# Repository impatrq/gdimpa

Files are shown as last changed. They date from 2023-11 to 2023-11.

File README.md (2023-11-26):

<div align="center">

# *GDIMPA*

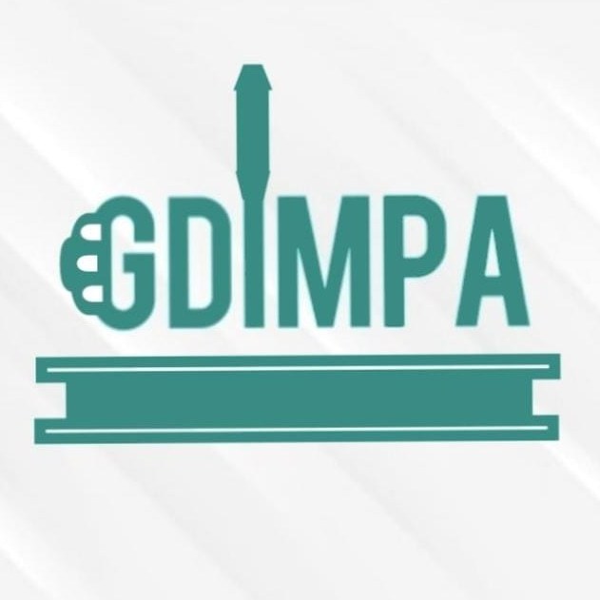
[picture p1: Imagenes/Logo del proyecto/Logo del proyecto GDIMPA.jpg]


&nbsp;

| Página web | linkedin | Instagram |
|---|---|---|
|[Mira nuestra pagina de Webnode](https://gdimpa-project-0.webnode.page)|[Búscanos en linkedin](https://www.linkedin.com/in/gd-impa-8b2537271/)|[También mira nuestro Instagram](https://www.instagram.com/GD.IMPA/?hl=es-la<%2Fp>)|

&nbsp;

</div>

## Objetivo:

Nuestro objetivo es la _modernización y puesta a punto_ de un _Grupo Electrógeno Diésel antiguo_, con esto buscamos brindar una forma _barata y sencilla_ de darle una nueva vida útil a estos equipos costosos, que no sean modernos, automatizándolos, de esta manera _controlar y monitorear_ el correcto funcionamiento de estos equipos.

## Descrición General:

*GDIMPA* es un sistema con la finalidad de _automatizar y monitorear_ de un generador eléctrico antiguo, el cual consta de la implementación de tres sensores:
- Un bulbo de temperatura: el cual es el encargado de medir la temperatura del motor, 
- Un bulbo de presión de aceite: el cual se encargade verificar si la presión del motor es la adecuada, 
- Un sensor de temperatura ambiental: el cual sirve para verificar si la temperatura ambiente es demasiado baja para que el motor encienda.

Todos los parámetros serán controlados en el tablero por dos PLC LOGO! 8, los cuales trabajan en conjunto para brindar una mayor capacidad de entradas tanto analógicas como digitales
Además se estará midiendo constantemente el amperaje y el voltaje generado, esto para ver que el equipo no esté trabajando de forma forzada.

El programa del PLC está hecho para controlar todos los parámetros y funciones de automatización, como el encendido automático, alarmas en caso de que la temperatura sea demasiado alta o la presión de aceite sea demasiado baja.

## Alcance:

El desarrollo de este sistema abarca a todas las industrias y personas que tengan un grupo electrógeno antiguo, pero que su funcionamiento aun sea bueno como un equipo auxiliar en caso de un corte en el suministro de corriente eléctrica, pero que al ser un equipo viejo no termine siendo práctico su uso. Sumándole a esto el hecho de que es más barato que el reemplazo total del equipo por uno nuevo con un panel automatizado.

## Tecnologías utilizadas

### sistemas embedidos

- PLC LOGO! 8

### Placas de desarrollo

- Arduino uno

### Software utilizados para el desarrollo

- LOGO!Soft Comfort v8.3
- Arduino IDE 2.1.1 (bibliotecas usadas Wire.h y LiquidCrystal_I2C.h)
- proteus 8
- CADE SIMU

### Página web

- webnode

### Periféricos utilizados

- Lm317t
- Lm324
- Lm35
- Relés
- Tetrapolar 4x25
- Contactor

### Planos

- AutoCAD

## ¿Quiénes somos?

Somos un grupo de alumnos de 7mo 1ra avionica de la E.E.S.T. N°7 "Taller Regional Quilmes" (IMPA).

## Integrantes

<div align="center">

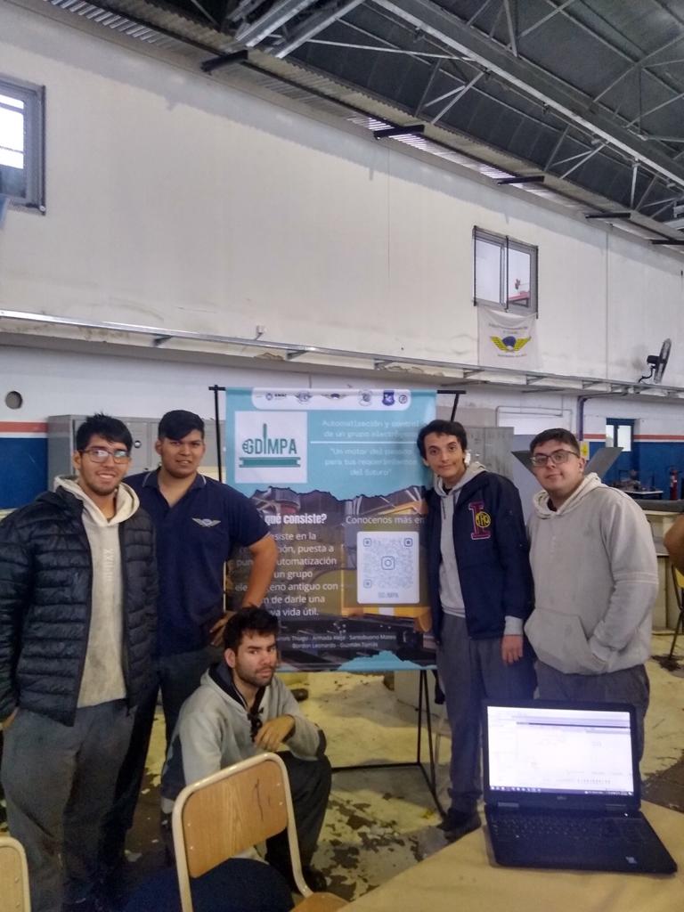
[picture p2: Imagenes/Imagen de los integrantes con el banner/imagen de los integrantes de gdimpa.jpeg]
Imagen de integrantes del proyecto


</div>

(De izquierda a derecha)

### Martins Thiago Ariel. 
Linkedin: (https://www.linkedin.com/in/thiago-a-martins/)

### Bordon Leonardo Agustin Caparros.
Linkedin: (https://www.linkedin.com/in/mateo-santobuono/?originalSubdomain=ar)

### Guzman Tomas Ignacio.
Linkedin: (https://www.linkedin.com/in/tomasignacio-guzman-9b542928a/)

### Armada Alejo.
Linkedin: (https://www.linkedin.com/in/alejo-armada/?originalSubdomain=ar)

### Santobuono Mateo Ruben.
Linkedin: (https://www.linkedin.com/in/mateo-santobuono/?originalSubdomain=ar)
****

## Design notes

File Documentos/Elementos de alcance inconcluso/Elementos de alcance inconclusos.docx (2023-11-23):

Elementos de alcance inconclusos

En este documento se encuentran todas las tareas las cuales teníamos pensado realizar y por diversas razones (ya sea falta de conocimientos, falta de tiempo, etc.) no se llegaron a completar:

- Reparación de la bomba inyectora: Desde principio de año hemos tenido problemas con la misma, fue el enfoque principal de trabajo durante la mayor parte del año. En un inicio al estar esta trabada la desarmamos y limpiamos, aunque a esta le rompimos una pieza gracias a la ayuda de un profesor se realizo una copia a medida, cuando la montamos esta no generaba suficiente presión y debido a falta tanto de conocimientos como de tiempo no fuimos capaces de ponerla en funcionamiento.
- Puesta en marcha del grupo electrógeno: Debido a que la bomba inyectora no se encontraba en condiciones, no emos sido capaces de poner en marcha el grupo electrógeno.
- Pantallas led: Debido al tiempo no tuvimos el tiempo de poner todas las pantallas en el tablero y tampoco de programarlas, tenemos las pantallas que fueron compradas por cooperadora.
- Bulbo de presión de aceite: Este componente lo tenemos desde principio de año, pero por mala gestión de nuestro tiempo no lo emos podido instalar en el sistema de aceite del propio motor, aunque se encuentra prácticamente cableado y listo para su instalación.
- Válvula electrónica para controlar el paso de combustible a la entrada de aire: Esta válvula era una idea originalmente concebida con el fin de hacer aun mas automático el sistema de calentamiento del motor, pero no nos concentramos en eso, aunque terminamos de cablear el sistema de timer para el calentamiento de la toma de aire.
- Control de zonas por prioridad: esta parte se encuentra programada, pero por la falta de tiempo no pudimos llevar el sistema al cableado, además de que las salidas del plc 2 fueron completamente usadas.
- Alarma de emergencia y botón para reiniciarla: El sistema se encuentra programado, e incluso hay una salida guardada para este sistema, la limitante es que no nos alcanzo el tiempo para agujerear el tablero y que nos faltó conseguir la luz.
- Bulbo de temperatura: este esta montado, pero falta el cableado, por que un día antes de la feria alguien rompió los cables que se encontraban unidos al bulbo.
- Los soportes para los trasformadores en el tablero: estos no fueron realizados, por falta de tiempo
- Realizar una estructura de protección: No la realizamos por falta de tiempo.
- Prendido completamente automático: Debido a limitaciones mecánicas no pudimos hacer 100% automático el encendido del motor.
- Incorporación de ruedas: Esta idea fue una que desde un inicio estuvo presente, aunque no fue nuestra prioridad y por eso no nos alcanzo el tiempo para terminarla.
- Apagado automático: Por falta de conocimientos sobre motores y también de tiempo, no logramos realizar esta idea, sino que fue reemplazada por una alarma en pantalla que muestra que se debe apagar el motor.
- Armado de los inyectores: Estos fueron sacados para su mantenimiento, y después por los problemas en la bomba no fue concretada su colocación.
- Cableado del interruptor de cambio de neutro para medición de los ojos de buey: Estos fueron colocados, pero no fueron cableados por escaso tiempo antes de la finalización de las partes.

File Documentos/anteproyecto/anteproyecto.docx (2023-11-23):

GDIMPA

GDIMPA:Este nombre fue elegido por el siguiente significado: Generador Diesel IMPA

Integrantes:

- Mateo santobuono
- Leonardo Bordon Caparros
- Tomas Ignacio Guzmán
- Alejo Armada
- Thiago Martins

Objetivo del proyecto:

Nuestro objetivo es proporcionar a la escuela con la capacidad de poder continuar con las actividades que requieran de electricidad en el caso de un apagón. Para lograr esto, restauraremos un generador diésel para que pueda volver a utilizarse como generador de energía de emergencia. También modernizaremos dicho generador para que este se prenda automáticamente desde el panel en el caso de un apagón y que pueda priorizar entre diferentes aparatos electrónicos a alimentar si es que no tiene la capacidad de alimentar a todos.

Utilidades del proyecto:

En el caso de un apagón, la escuela se vería incapaz de continuar con la enseñanza de ciertas materias que requieran de instrumentos electrónicos, tales como los osciloscopios, (Aquí hay que agregar más ejemplos), ect. Nuestro proyecto otorgaría la capacidad a la escuela de continuar con dichas enseñanzas sin ser interrumpida.

Descripción de funcionamiento

Nosotros proponemos como solución un sistema que mediante el uso de un PLC conectado a un motor diesel con un generador que proporcione energía a la escuela en el caso de un apagón o falta de energía.

Para lograr esto utilizaremos un Siemens LOGO! 8.2 que a través de varios voltímetros detectará si se ha producido un corte de luz para activar automáticamente desde el panel el motor diesel a través del generador, primero sensara la temperatura ambiente y en caso de ser necesario se activará el temporizador que calentará el aire para facilitar el encendido del motor.

La gestión de energía se realizará a través del programa del PLC que tendrá divisiones entre zonas más o menos prescindibles en el caso de que no sea posible alimentar a todas las zonas. Todo esto se mostrará en un panel de control, junto a los demás parámetros del motor. La temperatura del motor será leída a través de un sensor de temperatura y el nivel de combustible será leído con un sensor flotante.

Análisis de factibilidad:

El GDIMPA es un generador diésel que consta de un alternador trifásico tipo 2A2 y un panel de control.

Objetivos / Retos

Mateo Santo; Leonardo Bordón; Thiago Martins

(Mantenimiento / Limpieza)

1er paso: se encargará de la restauración y reemplazo de las piezas.

2do paso: una vez restaurado se decidirá que componentes deberán ser cambiados.

Tomas Ignacio Guzmán; Alejo Armada

(Diseño y programación)

1er paso: haremos un panel digital / analógico que nos permita la revisión para la automatización y control del arranque, consumo, etc.

2do paso: prueba y función del panel.

Tomas Ignacio; Alejo Armada; Leonardo Bordón; Mateo Santobuono; Martins Thiago

(Electricidad y electrónica)

1er paso: Circuitado para plc y otros circuitos necesarios para el proyecto.

2do paso: prueba y arranque de los circuitos para verificar su funcionamiento.

Costo del proyecto:

Componentes:

- Termocupla, $ 4730 ARG
- LM35, $ 785 ARG
- PLC simens Logo, $ 75950 ARG
- flotante nivel de combustible, 8140 ARG
- Líquido refrigerante 5 L, $6240 ARG
- Botones x 10, 600 ARG (cada uno)
- Display x 5, $500 ARG (cada uno)
- Batería 12v 180 Amper x 2, $71900 ARG (cada uno)

Costo total del proyecto: 244345$USD(la suma de todos los componentes)

Referencias:

https://www.microelectronicash.com/ofertas.php

https://www.elemon.net/

https://www.cdronline.com.ar/ofertas.php3

https://cika.com.ar/catalogo

Análisis de costo/beneficio:

Termocupla:Nos servirá para medir diferentes temperatura del motor del generador

LM35:Nos servirá para poder medir la temperatura ambiente

PLC Simens Logo:Nos servirá como el dispositivo que tendrá el programa que automatiza el generador de una manera robusta y confiable

Flotante nivel de combustible:Nos servirá para medir el nivel de combustible de el motor del generador

Líquido refrigerante:Nos servirá para refrigerar el motor del generador

Botones:Nos servirá para realizar diferentes secuencias en el motor como apagar/encender en el generador

Display:Nos servirá para mostrar diferentes parámetros del motor del generador

Batería:Nos servirá para poner en marcha el motor del generador

Diagrama en bloques del prototipo:

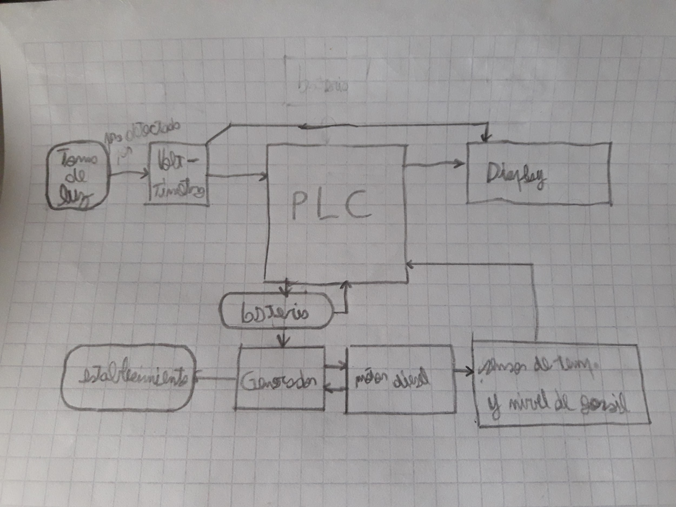
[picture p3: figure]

Voltímetros: Los voltímetros deben detectar si se ha producido un corte de luz

PLC: El PLC debe contener el programa que se encargará de procesar todos los datos, siendo estos los sensores, los voltímetros y los comandos del usuario, para prender el generador. También mostrará todos los datos en el display.

Display: En este se mostrarán todos los datos importantes, siendo la temperatura del motor y el nivel de gasoil. También permitirá al usuario prender el generador con solo apretar un botón.

Batería: Esta se utilizará para alimentar al PLC y al generador.

Generador: Se encargará de arrancar el motor y de generar energía a través del motor cuando este esté prendido.

Motor diesel: Cuando esté activo se encargará de hacer girar el alternador para que el generador pueda generar energía

Sensor de temp. y sensor de nivel de gasoil: Los sensores se encargarán de detectar la temp. y el nivel de gasoil. Estos parámetros serán leídos por el PLC y mostrados en el display.

Diagrama de tiempo de desarrollo:

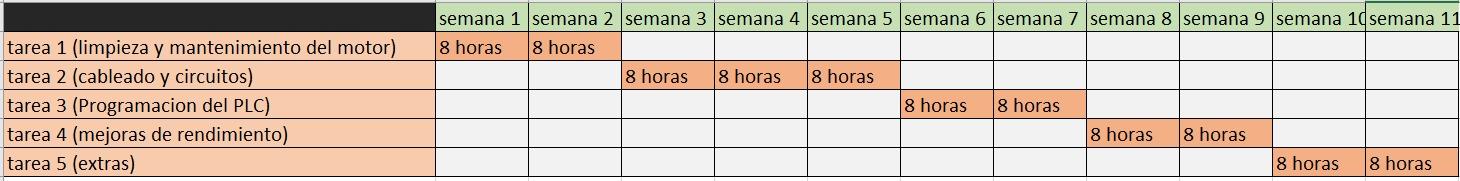
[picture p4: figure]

Escuela de Educación Técnica Nº7 Taller Regional Quilmes Prácticas Profesionalizantes: Especialidad Aviónica

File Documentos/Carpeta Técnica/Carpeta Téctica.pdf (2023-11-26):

2023

# Carpeta Técnica

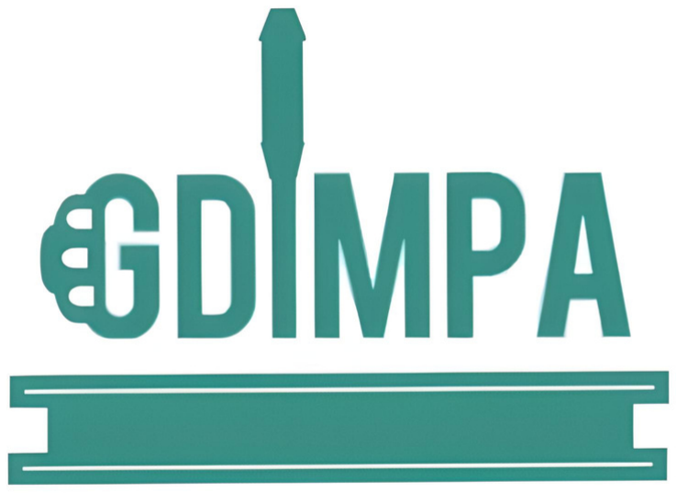
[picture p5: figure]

### 7° 1° Aviónica Comisión B

### E.E.S.T N°7 “T.R.Q”

## gd.impa (https://www.instagram.com/gd.impa/#)

# Índice

Presentación | Pág. 4
Objetivo | Pág. 6
Descripción General | Pág. 6
Alcance | Pág. 7
Segmento de destino | Pág. 7
Software | Pág. 8
Diagrama en bloques | Pág. 8
Lenguaje de programación | Pág. 9
Captura de código significativo | Pág. 9
Captura de interfaces visuales | Pág. 10
Sistemas embebidos | Pág. 12

## Placas de desarrollo Software utilizados para el desarrollo Código Periféricos utilizados Electrónica Software usado para el desarrollo de esquemáticos y PCB Diagrama eletríco del tablero PCBs Modelo 3D de placas PCB

### Pág. 13 Pág. 13 Pág. 14 Pág. 14 Pág. 15

### Pág. 16 Pág. 16 Pág. 17 Pág. 17

Placas terminada | Pág. 17

## Fuente de alimentación Especificación técnica de cada componente importante Estructura Software de diseño utilizado

### Pág. 19 Pág. 20 Pág. 20

Pagina web | Pág. 23
Acabado de la estructura | Pág. 23
Anexo | Pág. 24

## Integrantes:

Martins Thiago Abel, 7mo 1ra Aviónica Encargado del cableado y diseño de los circuitos

Armada Alejo, 7mo 1ra Aviónica
Programador del controlador lógico programable y demás controladores

Santobuono Mateo Ruben, 7mo 1ra Aviónica Encargado del marketin y presentaciones del proyecto

Bordon Caparrós Leonardo, 7mo 1ra Aviónica Encargado de las reparaciones y sistemas de control del grupo electrógeno

Guzmán Tomás, 7mo 1ra Aviónica
Diseñador grafico del proyecto y relaciones publicas

## Docentes Tutores:

Bianco, Carlos
Medina, Sergio
Palmieri, Diego

# Esfuerzo del Proyecto

34 Semanas de trabajo
25 hs de trabajo semanales en promedio de todos los integrantes

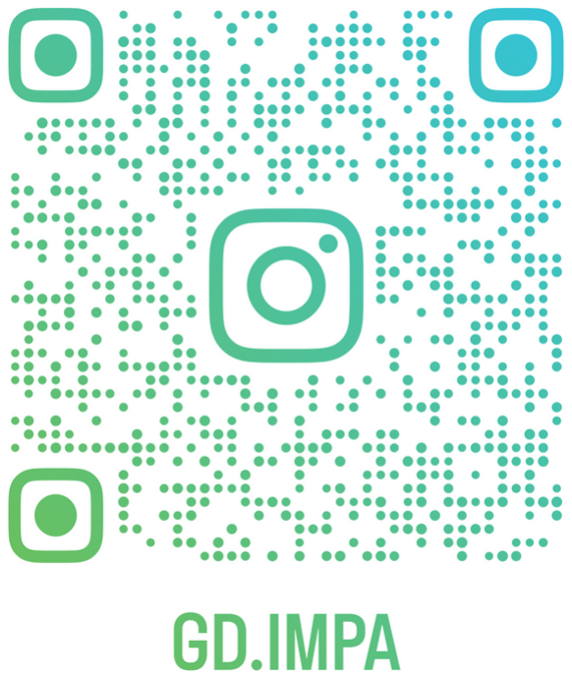
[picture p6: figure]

Instagram:

# Formas de encontrarnos

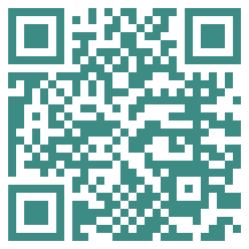
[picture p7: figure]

Linkedin:

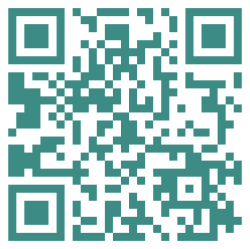
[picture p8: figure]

# Objetivo

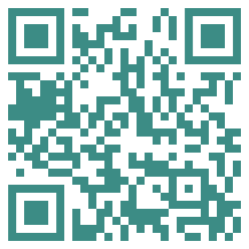
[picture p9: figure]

Modernización y puesta a punto de un Grupo Electrógeno Diésel antiguo, con esto buscamos brindar una forma barata y sencilla de darle una nueva vida útil a estos equipos costosos, que no sean modernos, automatizándolos, de esta manera controlar y monitoreando el correcto funcionamiento de estos equipos.

# Descrición General

Página web:

Git Hub:

Todos los parámetros serán controlados en el tablero por dos PLC LOGO! 8, los cuales trabajan en conjunto para brindar una mayor capacidad de entradas tanto analógicas como digitales, además se estará midiendo constantemente el amperaje y el voltaje generado, esto para ver que el equipo no esté trabajando de forma forzada. El programa del PLC está hecho para controlar todos los parámetros y funciones de automatización, como el encendido automático, alarmas en caso de que la temperatura sea demasiado alta o la presión de aceite sea demasiado baja.

# Alcance

El desarrollo de este sistema abarca a todas las industrias y personas que tengan un grupo electrógeno antiguo, pero que su funcionamiento aun sea bueno como un equipo auxiliar en caso de un corte en el suministro de corriente eléctrica, pero que al ser un equipo viejo no termine siendo práctico su uso. Sumándole a esto el hecho de que es más barato que el reemplazo total del equipo por uno nuevo con un panel automatizado.

# Segmento de destino

GDIMPA es un sistema con la finalidad de automatizar y monitoreo de un generador eléctrico antiguo, el cual consta de la implementación de tres sensores, un bulbo de temperatura, el cual es el encargado de medir la temperatura del motor, un bulbo de presión de aceite, el cual se encarga de verificar si la presión del motor es la adecuada, un sensor de temperatura ambiental, el cual sirve para verificar si la temperatura ambiente es demasiado baja para que el motor encienda, esto debido a que al ser un motor Diesel antiguo y no tener bujías a muy bajas temperaturas no es capaz de arrancar de la forma correcta.

# Diagrama en bloques

# Software

Nuestro segmento de destino son empresas y/o pacientes que necesitan constantemente de suministro eléctrico y no puedan parar por mucho tiempo su actividad, y que a su vez tengan un grupo electrógeno viejo que deseen seguir utilizándolo, para eso se podría aplicar nuestro proyecto, como una forma de barata y sencilla para la construcción del tablero eléctrico automatizado.

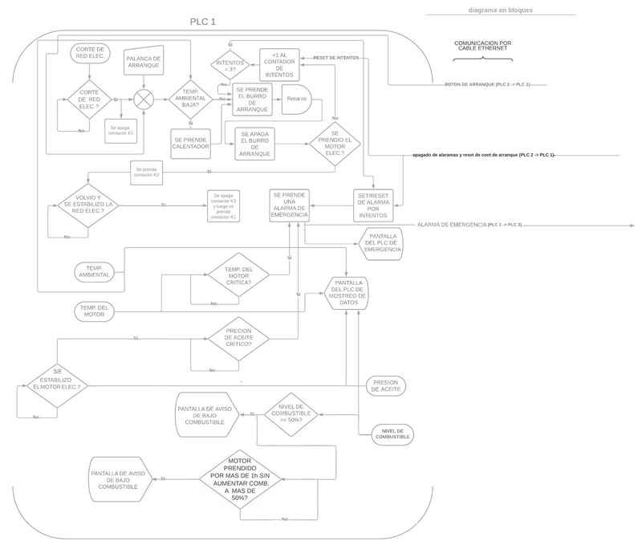
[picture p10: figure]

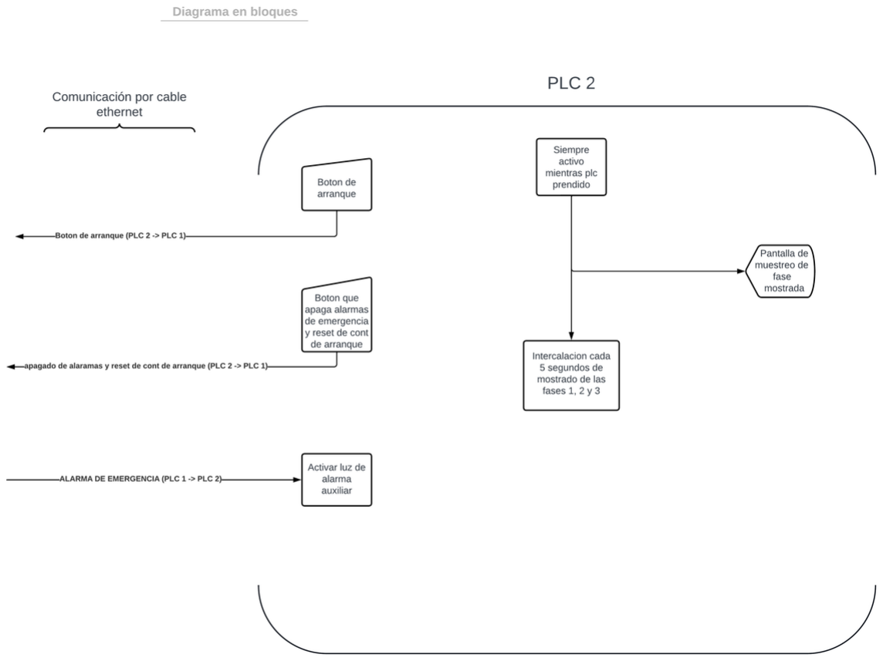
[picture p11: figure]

# Lenguaje de programación

Los lenguajes de programación utilizados en este caso fueron:

Programación en bloques de funciones: este tipo de programación consiste en usar compuertas lógicas (AND, OR, NAND, etc) conectando unas con otras y así darle forma al programa. Estos comandos o bloques representan distintas acciones individuales que pueden configurarse y/o combinarse con otros bloques para construir secuencias lógicas.

Programación en C++: En este tipo de programación se utiliza para indicar el control o el valor (INT,FLOAT,VOID,etc), de ciertos objetos, como el sensor, la pantalla LCD. Gracias a estos, también nos puede decir el resultados de operaciones, comparar datos, etc. Esta tiene que especificar el tipo que será el objeto para que se realice la compilación del código sin problema

# Captura de código significativo

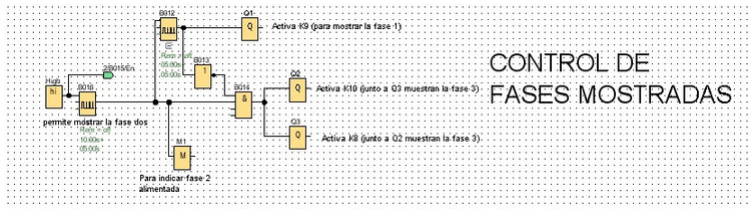
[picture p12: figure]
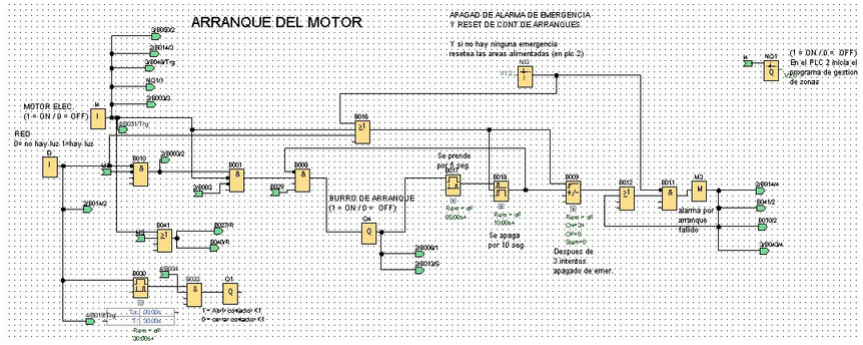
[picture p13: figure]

# Captura de interfaces visuales

Código de muestreo de fase del PLC 2: Este código es el encargado de activar y desactivar los contactores de una forma especifica para mostrar todas las fases a través de las pantallas ubicadas en la puerta del tablero eléctrico.

Código de arranque del motor del PLC 1: Este codigo es el encargado de arrancar el motor electrico en cuanto las las condiciones esten correctas (si temp ambiental baja, que se haya prendido el calentador), la red electrica este cortada y el operario presione el boton de arranque. Cuando se hayan cumplido todas las condiciones, el codigo prendera el burro de arranque por 5 segundos, y lo apagara por 10 segundos, si se prende el motor electrico, se dejara inmediatamente de prender el burro de arranque, pero si no se prende despues de 3 intentos se activara una alarma y dejara de prender el burro tambien. Se puede desactivar la alarma con un boton.

Pantalla de muestreo de fase de el plc 2: En esta pantalla se podrá observar un mensaje que indicará que fase se esta mostrando en la pantallas del tablero eléctrico. Esta pantalla vendrá acompañada de un fondo blanco. Se mostrará todo el tiempo en la pantalla del plc 2.

Pantalla de aviso de bajo combustible del PLC 1: En esta pantalla se podrá observar el nivel de combustible del motor. Esta pantalla vendrá acompañada de un fondo amarillo. Esta pantalla se mostrará por 5 segundos cada 5 segundos, interrumpiendo las pantallas de muestreo de datos, cuando el motor esté por debajo del 50% del combustible

Pantalla de muestreo de datos del PLC 1 número 1: En esta pantalla se podrá observar los datos de temperatura del motor, presión de aceite del motor y nivel de combustible del motor. Esta pantalla vendrá acompañada de un fondo blanco. Esta pantalla se mostrará en el PLC cuando no haya ningún aviso ni emergencia. Además esta pantalla se intercala con la pantalla de muestreo de datos del PLC 1 número 2 cada 10 segundos.

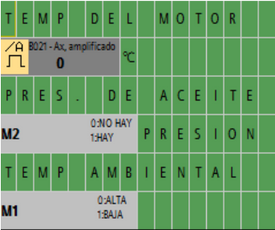
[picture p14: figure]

Pantalla de muestreo de datos del PLC 1 número 2: En esta pantalla se podrá observar los datos de temperatura del motor, presión de aceite del motor y si la temperatura ambiental es baja o no. Esta pantalla vendrá acompañada de un fondo blanco.Esta pantalla se mostrará en el PLC cuando no haya ningún aviso ni emergencia. Además esta pantalla se intercala con la pantalla de muestreo de datos del PLC 1 número 1 cada 10 segundos.

# Sistemas embebidos

El PLC LOGO! 8, como su nombre lo indica es un

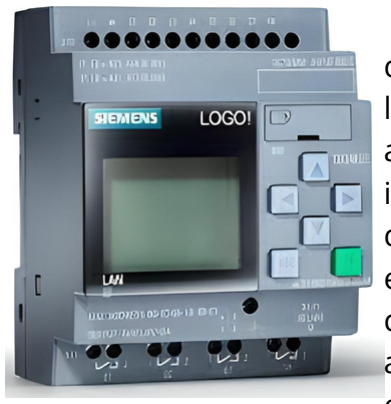
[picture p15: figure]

controlador lógico programable, con módulos lógicos inteligentes para proyectos de automatización a pequeña escala. La decisión de su implementación es debido a su robustez, confiabilidad y su fácil programación, Este modelo en concreto consta de 8 entradas digitales en total cuatro de las cuales pueden ser configuradas como analogicas, cuatro salidas con relés, un módulo externo para una tarjeta micro sd, se puede programar a través de un cable con conexión ethernet, cuenta con una pantalla display y la capacidad de programarlo sin conectarlo a la computadora con el uso de la pantalla y los botones de configuración que tiene.

Pantalla de emergencia del PLC 1: En esta pantalla se podrá observar los datos de temperatura del motor, presión de aceite del motor y una advertencia visual acerca de una falla en el motor. Esta pantalla vendrá acompañada de un fondo que intercala entre rojo y blanco. Esta pantalla se mostrará todo el tiempo cuando se esté detectando una falla del motor, interrumpiendo las pantallas de muestreo de datos.

Pantalla de advertencia de bajo combustible del PLC 1: En esta pantalla se podrá observar el nivel de combustible del motor. Esta pantalla vendrá acompañada de un fondo que intercala entre rojo y blanco. Esta pantalla se mostrará todo el tiempo, siempre y cuando no haya una falla del motor (temperatura crítica, presión de aceite crítico, etc), interrumpiendo las pantallas de muestreo de datos, cuando el motor esté por debajo del 50% del combustible por más de 1 hora de operación del motor.

# Software utilizados para el desarrollo

Uno de los software utilizados para el desarrollo es LOGO!Soft Comfort que es una plataforma desarrollada por la compañía Siemens, creadora de la familia de PLC LOGO!, permite programar los PLC de la misma familia a través de diagramas en bloques de funciones lógicas o ladder. Su uso es bastante sencillo e intuitivo, permite programar mediante el arrastre de bloques que se pueden interconectar entre sí para ir dándole forma al programa, permite la colocación de comentarios que pueden llegar a ser vitales para entender el funcionamiento de un programa, una vez que este se hace más complejo, además cuenta con una función de simulación que permite probar los programas antes de cargarlos en el PLC, agilizando en gran manera la resolución de problemas, ya que no hay que estar montando una y otra vez todo el circuito para ver cual es el error. La version utilizada del programa fue LOGO!Soft Comfort V8.3.

# Placas de desarrollo

Arduino uno, lo elegimos por que las cosas para la que lo usamos no requieren de una complejidad o un procesado muy alto, así que nos declinamos por este. Este modelo es un es una placa de microcontrolador de código abierto basado en el microchip ATmega328P. La placa está equipada con conjuntos de pines de E/S digitales y analógicas que pueden conectarse a varias placas de expansión y otros circuitos.

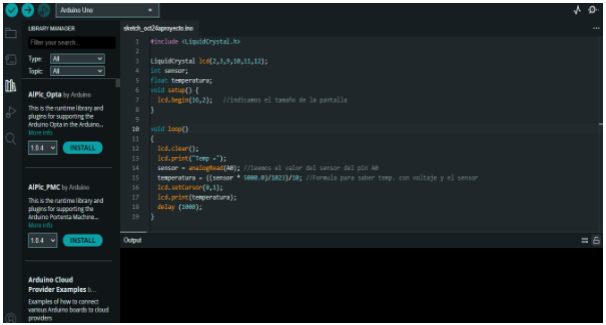
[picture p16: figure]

# Periféricos utilizados

Lm317t es un regulador de voltaje, con un encapsulado tipo mosfet. Este nos permite regular la tensión de salida con tan solo dos resistencias y permite una corriente de salida de hasta 1.5 amperes.

Otro de los software utilizados para el desarrollo es Arduino IDE (Integrated Development Environment), una aplicación de programación para las placas arduinos, esta subirá el código en el microcontrolador de la placa para poder interactuar con los sensores, luces led, pantallas LCD, etc. Este nos permite realizar códigos para la placa de manera sencilla, además de acceso a una librería muy extensa que nos podrá ayudar, siendo estos programas hechos por otras personas para facilitar la realización de nuestros proyectos independientes. La versión del programa utilizada fue Arduino IDE 2.1.1, y las bibliotecas usadas son Wire.h y LiquidCrystal_I2C.h

# Código

Este es el código para mostrar el valor de temperatura del LM35 a través de una pantalla LCD.

Contactor este dispositivo es un conmutador, que utiliza un bobinado para generar un campo magnético y así conmutar sus entradas, soporta 20 amperes en cada entrada y más de 220v

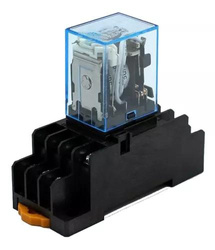
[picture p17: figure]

# Electrónica

Relés es un dispositivo electromagnético, que funciona como interruptor controlado por un circuito eléctrico, esto mediante un electroimán que al energizarse conmuta uno o más contactos y así funciona como un interruptor.

Tetrapolar 4x25 es una llave térmica, que interrumpe la corriente eléctrica, cuando hay un alto consumo o un cortocircuito. Capacidad de Ruptura: 3 KA, Polos: 4P, Bornes para cables hasta: hasta 16mm, Frecuencia : 50/60Hz, Amperaje: 4x25 y Tensión: 230/400v

Lm324 este dispositivo es un amplificador operacional, con un encapsulado DIP de 14 pines, la amplificación se puede regular con dos resistencias dependiendo si se quiere utilizar como un inversor o no inversor.

Lm35 es un sensor de temperatura con un encapsulado tipo transistor, con tres patas, tiene una variación o salto de 10 mv por cada grado centígrado

CADE SIMU es un pequeño programa el cual usamos para el diseño del circuito eléctrico en el tablero, este permite dibujar esquemas electrotécnicos, permitiendo insertar los distintos símbolos organizados en librerías de electricidad y electrónica, y a su vez trazar un circuito eléctrico de una forma fácil y rápida.

# Diagrama eletríco del tablero

# Software usado para el desarrollo de esquemáticos y PCB

El software usado para el desarrollo de las placas PCB fue proteus 8, es un sistema completo de diseño para circuitos electrónicos, el cual tiene un sistema de simulación mixto (analógico digital), además de un sistema que nos permite el diseño de una placa pcb de forma sencilla y la vista en 3D de la placa completa.

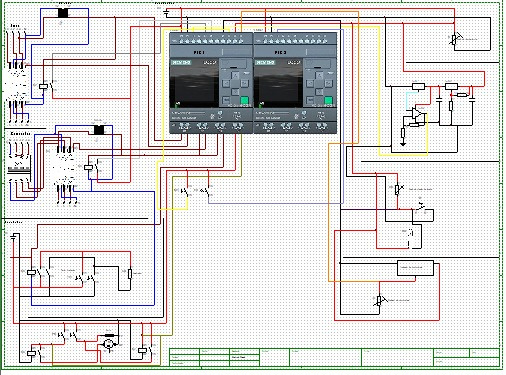
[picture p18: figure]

# PCBs

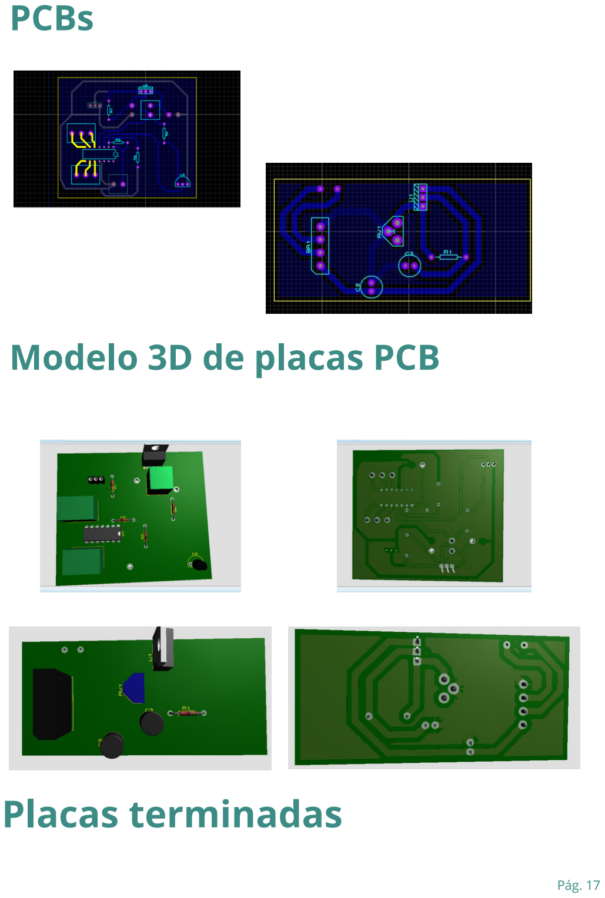
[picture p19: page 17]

# Modelo 3D de placas PCB

# Placas terminadas

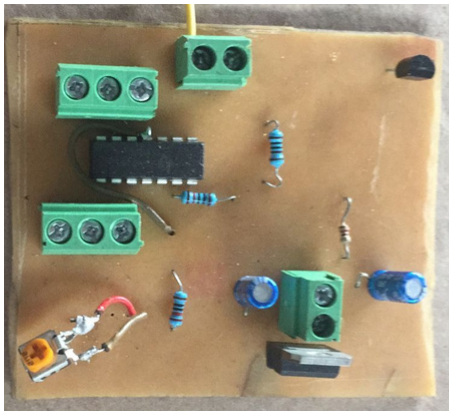
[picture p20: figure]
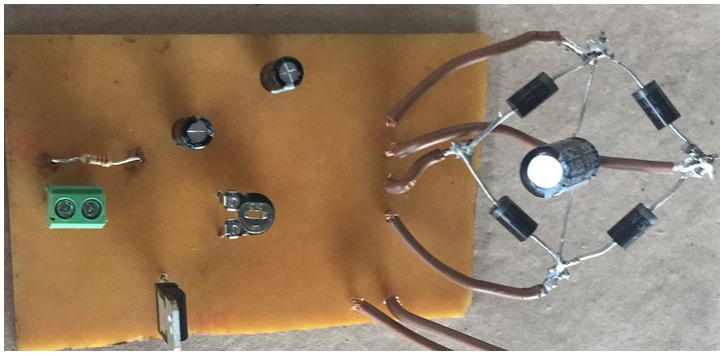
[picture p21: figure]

# Fuente de alimentación

La alimentación dentro de nuestro proyecto varía según la necesidad del circuito:

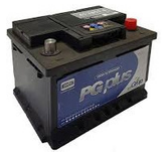
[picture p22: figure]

El tablero se alimenta con una batería de 12v 45Ah

Placa de simulación de parámetros de motor, se uso un puente de diodos, y un Lm317t

Placa de regulación de voltaje, amplificación y censado de temperatura, se uso un Lm35, un Lm324 y un Lm317t

# Especificación técnica de cada componente importante

Lm35

Rango de temperatura: -55° - 150° Tensión de alimentación: 4 V - 30 V.-Tipo de interfaz: Salida Análogica.

Transformador de 220v -24v de alterna y 100 W, en este caso este se encontrará conectado a la red electríca

El circuito de arranque del motor es alimentado por una batería de 12v 180Ah

Transformador de 220v -24v de alterna y 50 W, en este caso este se encontrará conectado a la salida del generador

# Estructura

Relés

Resistencia de contacto: 100 mOhm. Temperaturaambiente: -55° - 70°. Tiempo de operación y salida: 20 ms.

Lm324:

Número de canales: 4.
Rango de Temperatura: 0 - 70°. capacidad de 3 V - 32 V.
Arquitectura Bipolar.

Lm317t:

Corriente de salida superior a los 1,5 A. Salida ajustable de 12 V - 37 V. Limitación de corriente de cortocircuito.

Renderizado 3D de la estructura del tablero eléctrico dividido en tres secciones:
Soporté:

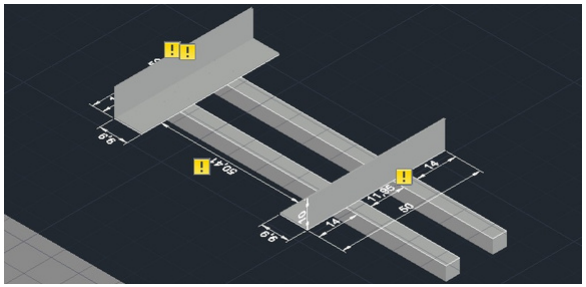
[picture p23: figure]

Sostiene el tablero a una altura cómoda para su uso, brindando una base estable y solida unida a la estructura del grupo electrógeno
Tapa del tablero:

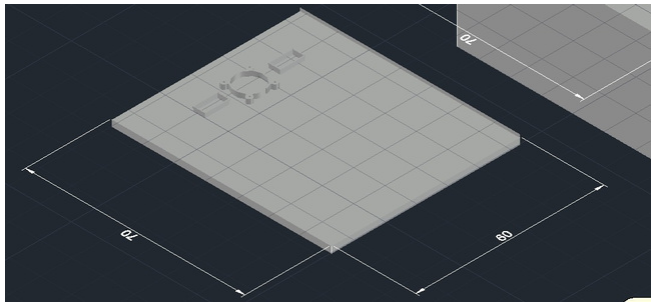
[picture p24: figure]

Una puerta rectangular de 70x60 cuya función principal es proteger el acceso de personal no autorizado en la manipulación interna del tablero de alta tensión, cuenta con instrumentos de indicación visual en el exterior.
Gabinete:

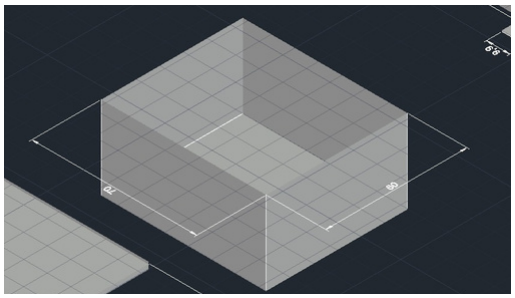
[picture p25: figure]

El gabinete, su principal función es la de contener el sistema de automatización eléctrico, evitando problemas con el mismo o una manipulación inadecuada que es peligrosa debido a que el circuito contiene alta tensión.

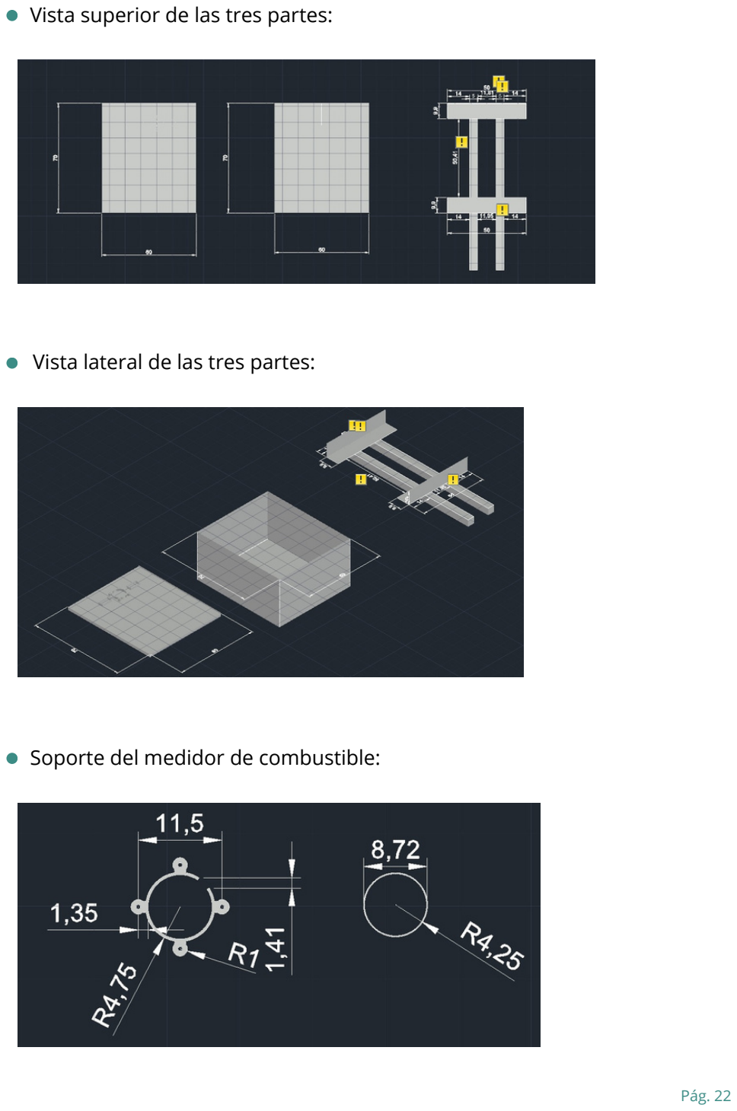
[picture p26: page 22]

Vista superior de las tres partes:

Vista lateral de las tres partes:

Soporte del medidor de combustible:


Creamos nuestra pagina web, utilizando Webnode, este es un sistema de creación de páginas web en línea desarrollado por Westcom s.r.o. Webnode utiliza la tecnología arrastrar y soltar, lo que permite que sea fácilmente utilizable y practico, permitiendo la creación de páginas web, blogs y tiendas en línea. El sistema es compatible con muchos navegadores, lo cual permite su facilidad de uso.

# Pagina web

# Software de diseño utilizado

AutoCAD es un software de diseño pensado para el diseño tanto en 3D como en 2D de diferentes estructuras. Se utiliza para dibujar, diseñar y modelar en 2D y 3D de forma precisa con sólidos, superficies, objetos de malla, características de documentación, etc. En nuestro caso es una plataforma que facilita el diseño de la estructura del tablero eléctrico que para tener mas en claro las limitaciones de espacio al incorporar los componentes electrónicos, y además para calcular con mas precisión la ubicación de los componentes para mantener una simetría en el tablero eléctricó.

# Acabado de la estructura

# Anexo

Introducción a la Programación del Módulo Lógico LOGO! https://www.udb.edu.sv/udb_files/recursos_guias/electronica-ingenieria/automatas-programables/2019/i/guia-1.pdf (https://www.udb.edu.sv/udb_files/recursos_guias/electronica-ingenieria/automatas-programables/2019/i/guia-1.pdf) Introducción a CADe SIMU
https://www.youtube.com/watch?v=_7oDXpPDQ78

Introducción a AUTOCAD
https://www.youtube.com/watch?v=5gpMPMTag9A

Introducción a WEBNODE
https://www.youtube.com/watch?v=EETmmN8-hdU

Introducción a Arduino
https://www.cursosaula21.com/arduino-todo-lo-que-necesitas-saber/ (https://www.cursosaula21.com/arduino-todo-lo-que-necesitas-saber/)

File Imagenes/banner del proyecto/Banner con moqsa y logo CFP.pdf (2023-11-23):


## ¿En qué consiste?

Consiste en la
restauración, puesta a
punto y automatización
de un grupo
electrógeno antiguo con
el fin de darle una
nueva vida útil.

Conocenos más en:

Automatización y control
de un grupo electrógeno

Martins Thiago - Armada Alejo - Santobuono Mateo Bordon Leonardo - Guzmán Tomás

“Un motor del pasado
para tus requerimientos
del futuro”

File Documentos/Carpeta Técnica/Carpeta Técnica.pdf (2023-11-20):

2023

# Carpeta Técnica


### 7° 1° Aviónica Comisión B

### E.E.S.T N°7 “T.R.Q”

## gd.impa (https://www.instagram.com/gd.impa/#)

# Índice

Presentación | Pág. 4
Objetivo | Pág. 6
Descripción General | Pág. 6
Alcance | Pág. 7
Segmento de destino | Pág. 7
Software | Pág. 8
Diagrama en bloques | Pág. 8
Lenguaje de programación | Pág. 9
Captura de código significativo | Pág. 9
Captura de interfaces visuales | Pág. 10
Sistemas embebidos | Pág. 12

## Placas de desarrollo Software utilizados para el desarrollo Código Periféricos utilizados Electrónica Software usado para el desarrollo de esquemáticos y PCB Diagrama eletríco del tablero PCBs Modelo 3D de placas PCB

### Pág. 13 Pág. 13 Pág. 14 Pág. 14 Pág. 15

### Pág. 16 Pág. 16 Pág. 17 Pág. 17

Placas terminada | Pág. 17

## Fuente de alimentación Especificación técnica de cada componente importante Estructura Software de diseño utilizado

### Pág. 19 Pág. 20 Pág. 20

Pagina web | Pág. 23
Acabado de la estructura | Pág. 23
Anexo | Pág. 24

## Integrantes:

Martins Thiago Abel, 7mo 1ra Aviónica Encargado del cableado y diseño de los circuitos

Armada Alejo, 7mo 1ra Aviónica
Programador del controlador lógico programable y demás controladores

Santobuono Mateo Ruben, 7mo 1ra Aviónica Encargado del marketin y presentaciones del proyecto

Bordon Caparrós Leonardo, 7mo 1ra Aviónica Encargado de las reparaciones y sistemas de control del grupo electrógeno

Guzmán Tomás, 7mo 1ra Aviónica
Diseñador grafico del proyecto y relaciones publicas

## Docentes Tutores:

Bianco, Carlos
Medina, Sergio
Palmieri, Diego

# Esfuerzo del Proyecto

34 Semanas de trabajo
25 hs de trabajo semanales en promedio de todos los integrantes


Instagram:

# Formas de encontrarnos


Linkedin:


# Objetivo


Modernización y puesta a punto de un Grupo Electrógeno Diésel antiguo, con esto buscamos brindar una forma barata y sencilla de darle una nueva vida útil a estos equipos costosos, que no sean modernos, automatizándolos, de esta manera controlar y monitoreando el correcto funcionamiento de estos equipos.

# Descrición General

Página web:

Git Hub:

Todos los parámetros serán controlados en el tablero por dos PLC LOGO! 8, los cuales trabajan en conjunto para brindar una mayor capacidad de entradas tanto analógicas como digitales, además se estará midiendo constantemente el amperaje y el voltaje generado, esto para ver que el equipo no esté trabajando de forma forzada. El programa del PLC está hecho para controlar todos los parámetros y funciones de automatización, como el encendido automático, alarmas en caso de que la temperatura sea demasiado alta o la presión de aceite sea demasiado baja.

# Alcance

El desarrollo de este sistema abarca a todas las industrias y personas que tengan un grupo electrógeno antiguo, pero que su funcionamiento aun sea bueno como un equipo auxiliar en caso de un corte en el suministro de corriente eléctrica, pero que al ser un equipo viejo no termine siendo práctico su uso. Sumándole a esto el hecho de que es más barato que el reemplazo total del equipo por uno nuevo con un panel automatizado.

# Segmento de destino

GDIMPA es un sistema con la finalidad de automatizar y monitoreo de un generador eléctrico antiguo, el cual consta de la implementación de tres sensores, un bulbo de temperatura, el cual es el encargado de medir la temperatura del motor, un bulbo de presión de aceite, el cual se encarga de verificar si la presión del motor es la adecuada, un sensor de temperatura ambiental, el cual sirve para verificar si la temperatura ambiente es demasiado baja para que el motor encienda, esto debido a que al ser un motor Diesel antiguo y no tener bujías a muy bajas temperaturas no es capaz de arrancar de la forma correcta.

# Diagrama en bloques

# Software

Nuestro segmento de destino son empresas y/o pacientes que necesitan constantemente de suministro eléctrico y no puedan parar por mucho tiempo su actividad, y que a su vez tengan un grupo electrógeno viejo que deseen seguir utilizándolo, para eso se podría aplicar nuestro proyecto, como una forma de barata y sencilla para la construcción del tablero eléctrico automatizado.



# Lenguaje de programación

Los lenguajes de programación utilizados en este caso fueron:

Programación en bloques de funciones: este tipo de programación consiste en usar compuertas lógicas (AND, OR, NAND, etc) conectando unas con otras y así darle forma al programa. Estos comandos o bloques representan distintas acciones individuales que pueden configurarse y/o combinarse con otros bloques para construir secuencias lógicas.

Programación en C++: En este tipo de programación se utiliza para indicar el control o el valor (INT,FLOAT,VOID,etc), de ciertos objetos, como el sensor, la pantalla LCD. Gracias a estos, también nos puede decir el resultados de operaciones, comparar datos, etc. Esta tiene que especificar el tipo que será el objeto para que se realice la compilación del código sin problema

# Captura de código significativo


# Captura de interfaces visuales

Código de muestreo de fase del PLC 2: Este código es el encargado de activar y desactivar los contactores de una forma especifica para mostrar todas las fases a través de las pantallas ubicadas en la puerta del tablero eléctrico.

Código de arranque del motor del PLC 1: Este codigo es el encargado de arrancar el motor electrico en cuanto las las condiciones esten correctas (si temp ambiental baja, que se haya prendido el calentador), la red electrica este cortada y el operario presione el boton de arranque. Cuando se hayan cumplido todas las condiciones, el codigo prendera el burro de arranque por 5 segundos, y lo apagara por 10 segundos, si se prende el motor electrico, se dejara inmediatamente de prender el burro de arranque, pero si no se prende despues de 3 intentos se activara una alarma y dejara de prender el burro tambien. Se puede desactivar la alarma con un boton.

Pantalla de muestreo de fase de el plc 2: En esta pantalla se podrá observar un mensaje que indicará que fase se esta mostrando en la pantallas del tablero eléctrico. Esta pantalla vendrá acompañada de un fondo blanco. Se mostrará todo el tiempo en la pantalla del plc 2.

Pantalla de aviso de bajo combustible del PLC 1: En esta pantalla se podrá observar el nivel de combustible del motor. Esta pantalla vendrá acompañada de un fondo amarillo. Esta pantalla se mostrará por 5 segundos cada 5 segundos, interrumpiendo las pantallas de muestreo de datos, cuando el motor esté por debajo del 50% del combustible

Pantalla de muestreo de datos del PLC 1 número 1: En esta pantalla se podrá observar los datos de temperatura del motor, presión de aceite del motor y nivel de combustible del motor. Esta pantalla vendrá acompañada de un fondo blanco. Esta pantalla se mostrará en el PLC cuando no haya ningún aviso ni emergencia. Además esta pantalla se intercala con la pantalla de muestreo de datos del PLC 1 número 2 cada 10 segundos.


Pantalla de muestreo de datos del PLC 1 número 2: En esta pantalla se podrá observar los datos de temperatura del motor, presión de aceite del motor y si la temperatura ambiental es baja o no. Esta pantalla vendrá acompañada de un fondo blanco.Esta pantalla se mostrará en el PLC cuando no haya ningún aviso ni emergencia. Además esta pantalla se intercala con la pantalla de muestreo de datos del PLC 1 número 1 cada 10 segundos.

# Sistemas embebidos

El PLC LOGO! 8, como su nombre lo indica es un


controlador lógico programable, con módulos lógicos inteligentes para proyectos de automatización a pequeña escala. La decisión de su implementación es debido a su robustez, confiabilidad y su fácil programación, Este modelo en concreto consta de 8 entradas digitales en total cuatro de las cuales pueden ser configuradas como analogicas, cuatro salidas con relés, un módulo externo para una tarjeta micro sd, se puede programar a través de un cable con conexión ethernet, cuenta con una pantalla display y la capacidad de programarlo sin conectarlo a la computadora con el uso de la pantalla y los botones de configuración que tiene.

Pantalla de emergencia del PLC 1: En esta pantalla se podrá observar los datos de temperatura del motor, presión de aceite del motor y una advertencia visual acerca de una falla en el motor. Esta pantalla vendrá acompañada de un fondo que intercala entre rojo y blanco. Esta pantalla se mostrará todo el tiempo cuando se esté detectando una falla del motor, interrumpiendo las pantallas de muestreo de datos.

Pantalla de advertencia de bajo combustible del PLC 1: En esta pantalla se podrá observar el nivel de combustible del motor. Esta pantalla vendrá acompañada de un fondo que intercala entre rojo y blanco. Esta pantalla se mostrará todo el tiempo, siempre y cuando no haya una falla del motor (temperatura crítica, presión de aceite crítico, etc), interrumpiendo las pantallas de muestreo de datos, cuando el motor esté por debajo del 50% del combustible por más de 1 hora de operación del motor.

# Software utilizados para el desarrollo

Uno de los software utilizados para el desarrollo es LOGO!Soft Comfort que es una plataforma desarrollada por la compañía Siemens, creadora de la familia de PLC LOGO!, permite programar los PLC de la misma familia a través de diagramas en bloques de funciones lógicas o ladder. Su uso es bastante sencillo e intuitivo, permite programar mediante el arrastre de bloques que se pueden interconectar entre sí para ir dándole forma al programa, permite la colocación de comentarios que pueden llegar a ser vitales para entender el funcionamiento de un programa, una vez que este se hace más complejo, además cuenta con una función de simulación que permite probar los programas antes de cargarlos en el PLC, agilizando en gran manera la resolución de problemas, ya que no hay que estar montando una y otra vez todo el circuito para ver cual es el error.

# Placas de desarrollo

Arduino uno, lo elegimos por que las cosas para la que lo usamos no requieren de una complejidad o un procesado muy alto, así que nos declinamos por este. Este modelo es un es una placa de microcontrolador de código abierto basado en el microchip ATmega328P. La placa está equipada con conjuntos de pines de E/S digitales y analógicas que pueden conectarse a varias placas de expansión y otros circuitos.


# Periféricos utilizados

Lm317t es un regulador de voltaje, con un encapsulado tipo mosfet. Este nos permite regular la tensión de salida con tan solo dos resistencias y permite una corriente de salida de hasta 1.5 amperes.

Otro de los software utilizados para el desarrollo es Arduino IDE (Integrated Development Environment), una aplicación de programación para las placas arduinos, esta subirá el código en el microcontrolador de la placa para poder interactuar con los sensores, luces led, pantallas LCD, etc. Este nos permite realizar códigos para la placa de manera sencilla, además de acceso a una librería muy extensa que nos podrá ayudar, siendo estos programas hechos por otras personas para facilitar la realización de nuestros proyectos independientes

# Código

Este es el código para mostrar el valor de temperatura del LM35 a través de una pantalla LCD.

Contactor este dispositivo es un conmutador, que utiliza un bobinado para generar un campo magnético y así conmutar sus entradas, soporta 20 amperes en cada entrada y más de 220v


# Electrónica

Relés es un dispositivo electromagnético, que funciona como interruptor controlado por un circuito eléctrico, esto mediante un electroimán que al energizarse conmuta uno o más contactos y así funciona como un interruptor.

Tetrapolar 4x25 es una llave térmica, que interrumpe la corriente eléctrica, cuando hay un alto consumo o un cortocircuito. Capacidad de Ruptura: 3 KA, Polos: 4P, Bornes para cables hasta: hasta 16mm, Frecuencia : 50/60Hz, Amperaje: 4x25 y Tensión: 230/400v

Lm324 este dispositivo es un amplificador operacional, con un encapsulado DIP de 14 pines, la amplificación se puede regular con dos resistencias dependiendo si se quiere utilizar como un inversor o no inversor.

Lm35 es un sensor de temperatura con un encapsulado tipo transistor, con tres patas, tiene una variación o salto de 10 mv por cada grado centígrado

CADE SIMU es un pequeño programa el cual usamos para el diseño del circuito eléctrico en el tablero, este permite dibujar esquemas electrotécnicos, permitiendo insertar los distintos símbolos organizados en librerías de electricidad y electrónica, y a su vez trazar un circuito eléctrico de una forma fácil y rápida.

# Diagrama eletríco del tablero

# Software usado para el desarrollo de esquemáticos y PCB

El software usado para el desarrollo de las placas PCB fue proteus 8, es un sistema completo de diseño para circuitos electrónicos, el cual tiene un sistema de simulación mixto (analógico digital), además de un sistema que nos permite el diseño de una placa pcb de forma sencilla y la vista en 3D de la placa completa.


# PCBs


# Modelo 3D de placas PCB

# Placas terminadas


# Fuente de alimentación

La alimentación dentro de nuestro proyecto varía según la necesidad del circuito:


El tablero se alimenta con una batería de 12v 45Ah

Placa de simulación de parámetros de motor, se uso un puente de diodos, y un Lm317t

Placa de regulación de voltaje, amplificación y censado de temperatura, se uso un Lm35, un Lm324 y un Lm317t

# Especificación técnica de cada componente importante

Lm35

Rango de temperatura: -55° - 150° Tensión de alimentación: 4 V - 30 V.-Tipo de interfaz: Salida Análogica.

Transformador de 220v -24v de alterna y 100 W, en este caso este se encontrará conectado a la red electríca

El circuito de arranque del motor es alimentado por una batería de 12v 180Ah

Transformador de 220v -24v de alterna y 50 W, en este caso este se encontrará conectado a la salida del generador

# Estructura

Relés

Resistencia de contacto: 100 mOhm. Temperaturaambiente: -55° - 70°. Tiempo de operación y salida: 20 ms.

Lm324:

Número de canales: 4.
Rango de Temperatura: 0 - 70°. capacidad de 3 V - 32 V.
Arquitectura Bipolar.

Lm317t:

Corriente de salida superior a los 1,5 A. Salida ajustable de 12 V - 37 V. Limitación de corriente de cortocircuito.

Renderizado 3D de la estructura del tablero eléctrico dividido en tres secciones:
Soporté:


Sostiene el tablero a una altura cómoda para su uso, brindando una base estable y solida unida a la estructura del grupo electrógeno
Tapa del tablero:


Una puerta rectangular de 70x60 cuya función principal es proteger el acceso de personal no autorizado en la manipulación interna del tablero de alta tensión, cuenta con instrumentos de indicación visual en el exterior.
Gabinete:


El gabinete, su principal función es la de contener el sistema de automatización eléctrico, evitando problemas con el mismo o una manipulación inadecuada que es peligrosa debido a que el circuito contiene alta tensión.


Vista superior de las tres partes:

Vista lateral de las tres partes:

Soporte del medidor de combustible:


Creamos nuestra pagina web, utilizando Webnode, este es un sistema de creación de páginas web en línea desarrollado por Westcom s.r.o. Webnode utiliza la tecnología arrastrar y soltar, lo que permite que sea fácilmente utilizable y practico, permitiendo la creación de páginas web, blogs y tiendas en línea. El sistema es compatible con muchos navegadores, lo cual permite su facilidad de uso.

# Pagina web

# Software de diseño utilizado

AutoCAD es un software de diseño pensado para el diseño tanto en 3D como en 2D de diferentes estructuras. Se utiliza para dibujar, diseñar y modelar en 2D y 3D de forma precisa con sólidos, superficies, objetos de malla, características de documentación, etc. En nuestro caso es una plataforma que facilita el diseño de la estructura del tablero eléctrico que para tener mas en claro las limitaciones de espacio al incorporar los componentes electrónicos, y además para calcular con mas precisión la ubicación de los componentes para mantener una simetría en el tablero eléctricó.

# Acabado de la estructura

# Anexo

Introducción a la Programación del Módulo Lógico LOGO! https://www.udb.edu.sv/udb_files/recursos_guias/electronica-ingenieria/automatas-programables/2019/i/guia-1.pdf (https://www.udb.edu.sv/udb_files/recursos_guias/electronica-ingenieria/automatas-programables/2019/i/guia-1.pdf) Introducción a CADe SIMU
https://www.youtube.com/watch?v=_7oDXpPDQ78

Introducción a AUTOCAD
https://www.youtube.com/watch?v=5gpMPMTag9A

Introducción a WEBNODE
https://www.youtube.com/watch?v=EETmmN8-hdU

Introducción a Arduino
https://www.cursosaula21.com/arduino-todo-lo-que-necesitas-saber/ (https://www.cursosaula21.com/arduino-todo-lo-que-necesitas-saber/)

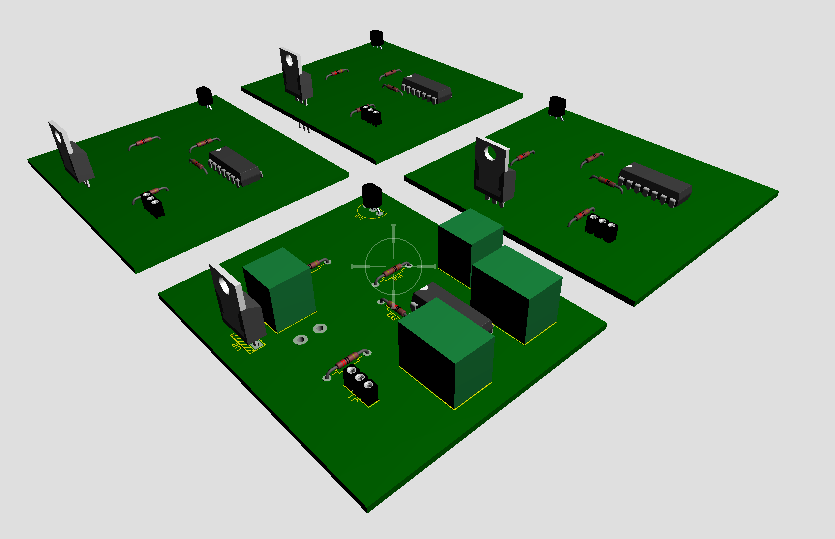
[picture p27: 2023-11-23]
Proteus/Diseño de placa de regulador de voltaje y sensor de temperatura/3D vista lateral de la placa de regulacion de voltaje y sensor de temperatura.png

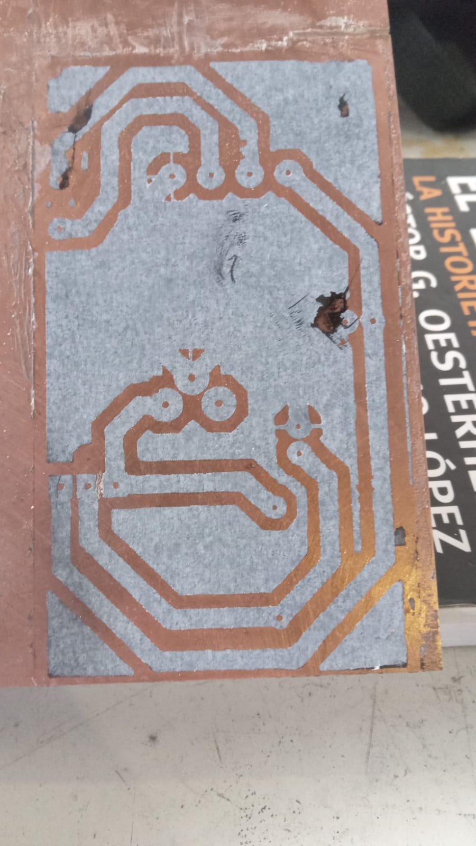
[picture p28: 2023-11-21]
Proteus/Diseño de la placa rectificadora/preparación de la placa rectificadora.jpeg

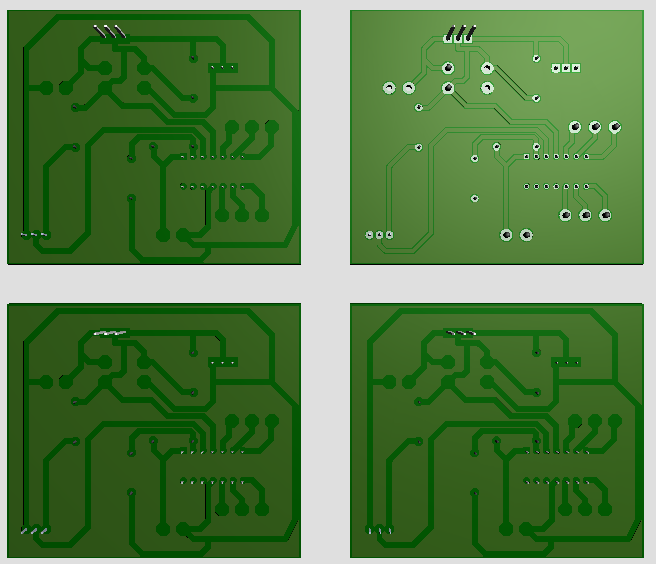
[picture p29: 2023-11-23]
Proteus/Diseño de placa de regulador de voltaje y sensor de temperatura/3D 3D vista inferior de la placa de regulacion de voltaje y sensor de temperatura.png

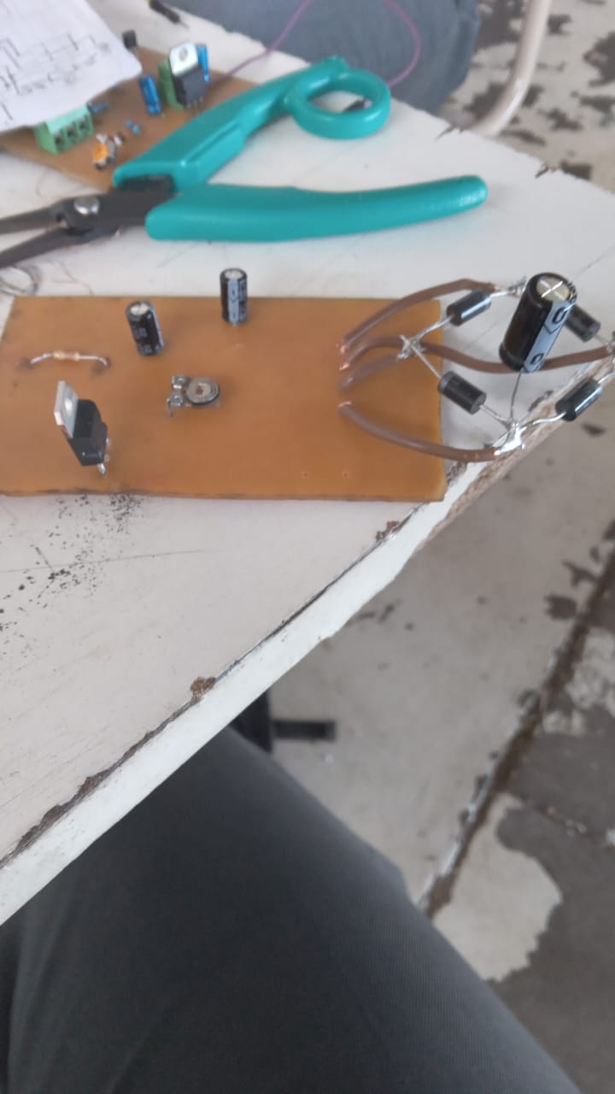
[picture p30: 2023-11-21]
Proteus/Diseño de la placa rectificadora/terminado de la placa rectificadora.jpeg

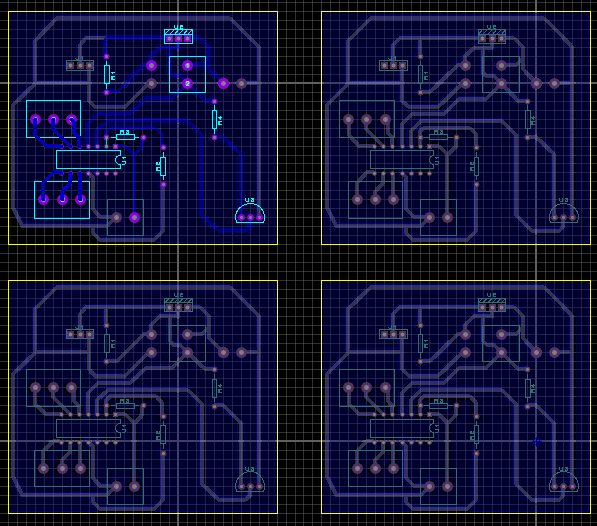
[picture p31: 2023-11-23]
Proteus/Diseño de placa de regulador de voltaje y sensor de temperatura/PCB de la placa de regulacion de voltaje y sensor de temperatura.png

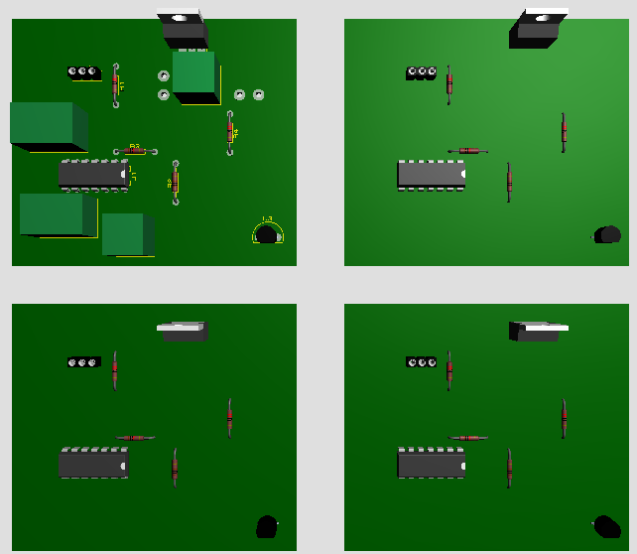
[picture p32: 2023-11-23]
Proteus/Diseño de placa de regulador de voltaje y sensor de temperatura/3D vista superior de la placa de regulacion de voltaje y sensor de temperatura.png

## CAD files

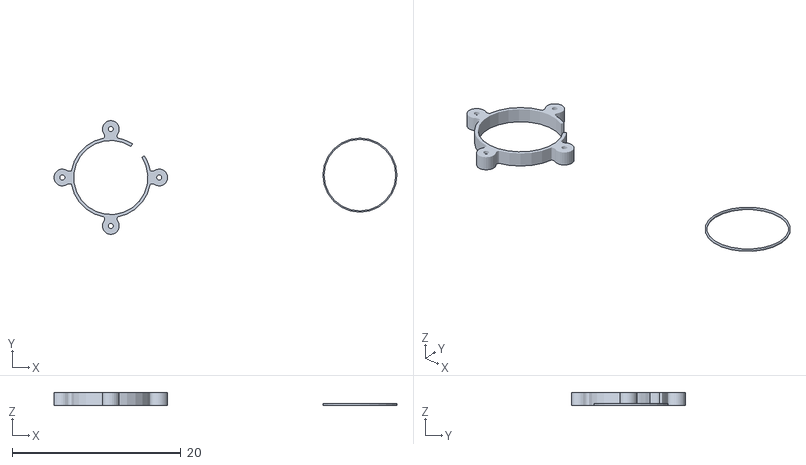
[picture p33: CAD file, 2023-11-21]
AutoCAD/Modelados 3D/modelado 3D del medidor de combustible/Soporte reloj de combustile.stl
40.7 x 13.5 x 1.50

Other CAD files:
AutoCAD/Modelados 3D/modelado 3D del tablero electrico/tablero y soporte.dwg
AutoCAD/Modelados 3D/modelado 3D del medidor de combustible/Soporte reloj de combustile.dwg

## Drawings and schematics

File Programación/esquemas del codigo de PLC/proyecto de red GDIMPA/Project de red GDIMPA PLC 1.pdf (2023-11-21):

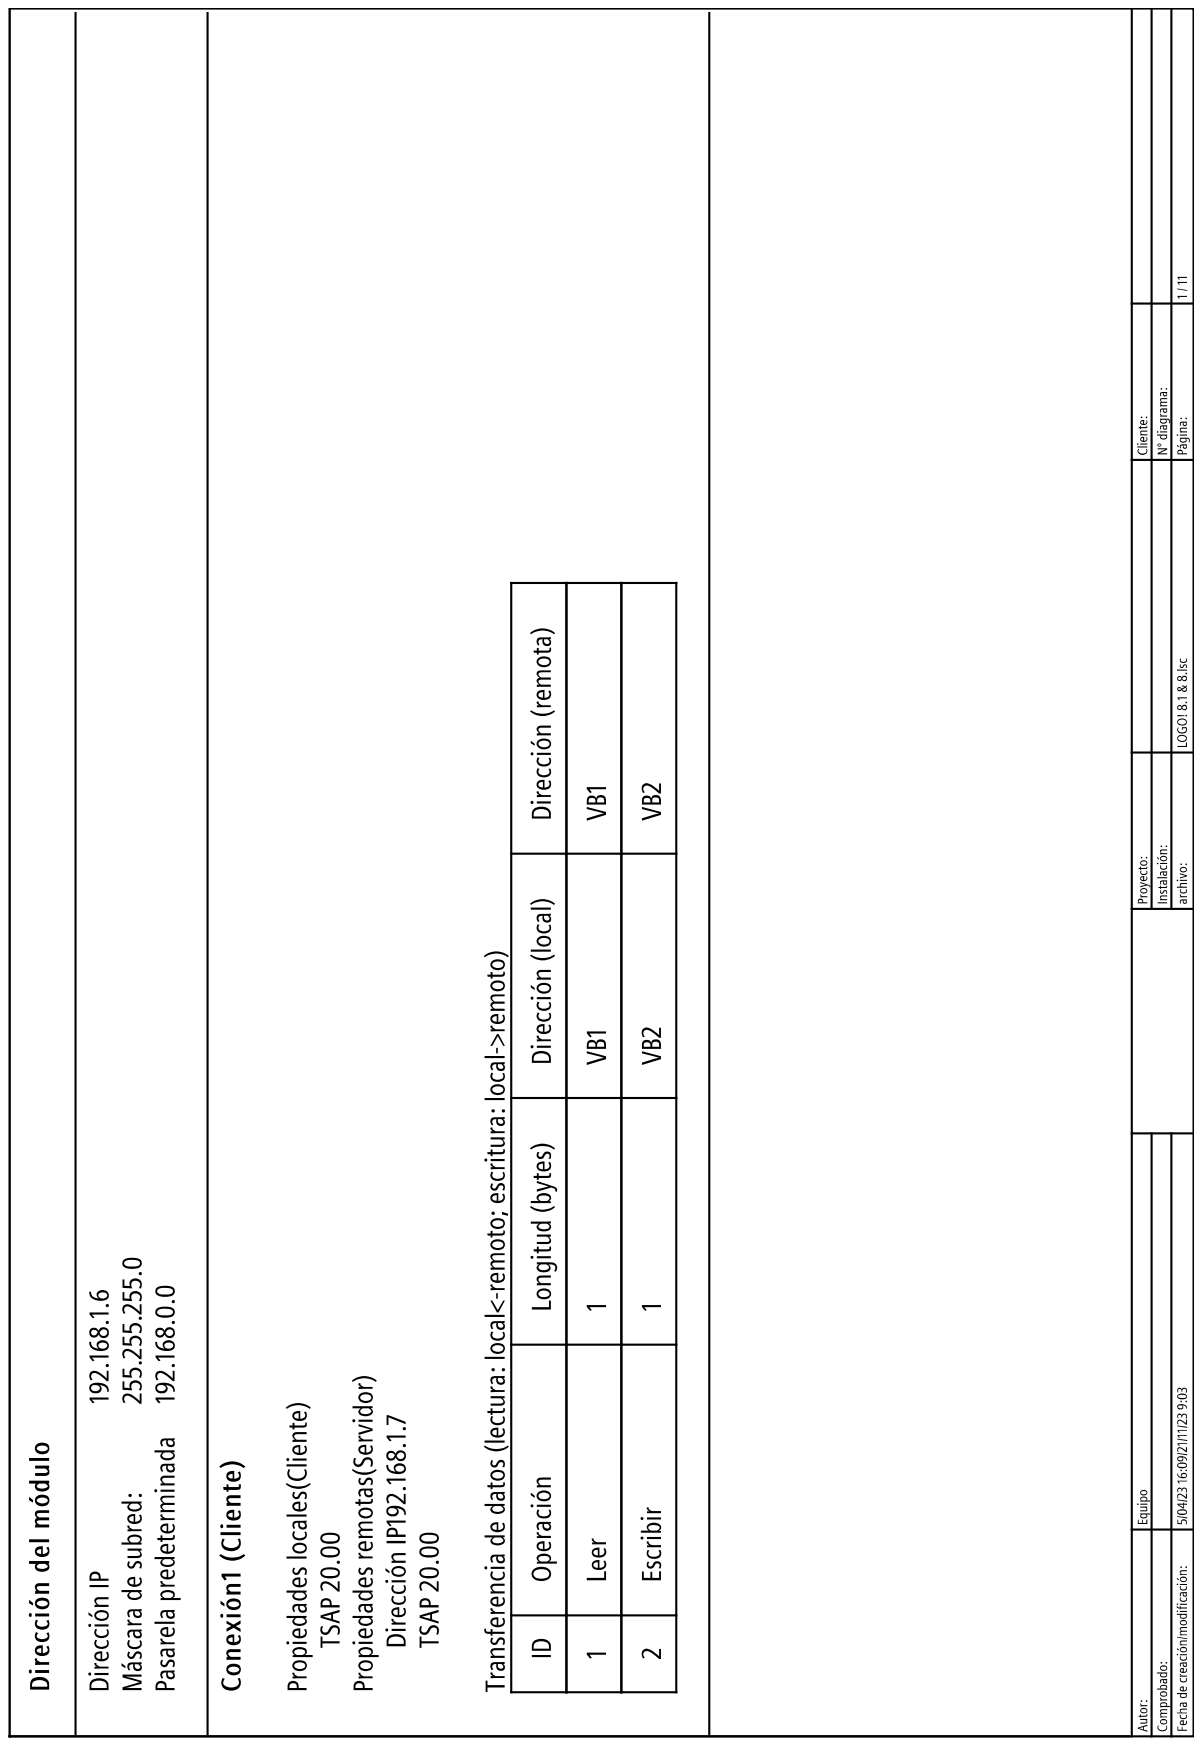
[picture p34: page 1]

I3 Q4 BURRO DE ARRANQUE (1 = ON / 0 = OFF) B001 RED 0= no hay luz 1=hay luz I4 MOTOR ELEC. (1 = ON / 0 = OFF) B008 RCnt Dir ParB009 Rem = off On=3+ Off=0 Start=0 B010 B011 B012 B016 TrgT B017 Rem = off 05:00s+ TrgRT B018 Rem = off 10:00s+ I5 PALANCA DE ARRANQUE (1 = ON / 0 = OFF) SRParB040 Rem = off B041 NQ1 V2.0 NQ1/1 I4 NI2 V1.1 BOTON QUE PERMITE EL ARRANQUE (1 = ON / 0 = OFF)(viene del PLC 2) B026 SRParB027 Rem = off Se prende por 5 seg Se apaga por 10 seg Despues de 3 intentos apagado de emer. (1 = ON / 0 = OFF) En el PLC 2 inicia el programa de gestion de zonas Lo mantiene precionado hasta que prenda el motor Lo mantiene precionado hasta que prenda el motor 3/B048/Trg 2/B006/1 2/B013/S 2/B003/2 2/B003 2/B014/3 2/B003/3 B041 B027/R B041 B040/R ARRANQUE DEL MOTORBOTON Y PALANCA DE ARRANQUE 3/B050/2 Q1 1 = Abrir contactor K1 0 = cerrar contactor K1 2/B014/2 M3 alarma por arranque fallido 2/B014/4 M3 B010/2 M3 B041/2 3/B043/4 B029 2/B003/4 2/B007/2 B040 B029/1 B029 B008/4 TrgT B030 Rem = off 30:00m+ Ta: 00:00m T: 30:00m 4/B019/Trg 4/B031/Trg B032 4/B034 NI3 V1.2 APAGAD DE ALARMA DE EMERGENCIA Y RESET DE CONT DE ARRANQUES Y si no hay ninguna emergencia resetea las areas alimentadas (en plc 2) 3/B022/2 3/B022/1

B003 Q3 CALENTADOR (1 = ON / 0 = OFF)TrgT B005 Rem = off 30:00s+ B006 SRParB013 Rem = off B014 B007 AI3 TEMP AMBIENTALAx ParB042 Gain=1.0+ Offset=0 On=0 Off=279 Point=0 B042 en la salida del amp del LM35 = 110 mV por grado / max 8,92 V (en 80°c) en el PLC = si 1000 -> 10V 1 -> 10 mV se activa a 20 se desactiva a 25 20°C -> aprox 2,24V -> 224 25 °C -> aprox 2,79V -> 279 M1PARA INDICAR SI LA TEMP AMB ES BAJA O NO Se prende el calentador por 30 seg 1/Q4 1/Q4 1/B010 1/B001/3 1/I4 1/I4 SENSOR DE TEMP AMB y CALENTADOR 1/I3 1/M3 1/B040 1/B040

AI1 BULBO DE TEMP DEL MOTOR Ax ParB021 Gain=1.0+ Offset=0 On=24 Off=24 Point=0 On: 24 Off: 24 Ax: 0 En Inv ParB024 Rem = off 01:00s+ 01:00s M29 (LOGO! se retroilumina en rojo) EnP ParB023 Prio = 123 Quit = off Text1: enabled Text2: disabled B043 Ax ParB004 Gain =0.1+ Offset=0 Point =1 Ax: 0 Transforma el valor de 0 - 1000 a 0 - 100Si supera los 24° se activa la alarma titila en rojo en caso de alarma pantalla de alarma Ax ParB025 Gain=1.0+ Offset=0 On=1 Off=0 Point=0 EnP ParB037 Prio = 99 Quit = off Text1: enabled Text2: disabled pantalla de aviso de bajo combustible si el combustible esta menor de 50% B044 Ax ParB045 Gain =0.1+ Offset=0 Point =1 Ax: 0 Transforma el valor de 0 - 1000 a 0 - 100 En Inv ParB046 Rem = off 05:00s+ 05:00s EnP ParB047 Prio = 101 Quit = off Text1: enabled Text2: disabled pantalla de ALARMA de bajo combustible M28 (LOGO! se retroilumina en ámbar) B039 B044 B039/1 B047 B044/2 AI2 NIVEL DE COMBUSTIBLE M2 PARA INDICAR SI HAY PRESION O NO B002 TrgT B048 Rem = off 05:00s+ DESPUES DE QUE SE HAYA PRENDIDO EL MOTOR POR MAS DE 5 SEG SE EMPIEZA A CHEQUEAR LA PRESION DE ACEITE 1/I4 B043/2 B002 B021 B043/1 BULBO DE TEMPBULBO DE PRESION DE ACEITE NIVEL DE COMBUSTIBLE PANTALLA DE ALARMA REn Ral ParB049 MI= 1h 0m+ OT= 0h 0m Q->0=R Ax ParB038 Gain=1.0+ Offset=0 On=1 Off=0 Point=0 si el combustible es mayor a 50% B050 1/I4 M4 posible bajo combustible B051 NI1 V1.0 (1 = ON / 0 = OFF) Activa la emerg. en caso de falta de carga incluso con solo una zona (PLC 2) NQ3 V2.2 1/M3 Salida de alarma a plc 2 I6 Bulbo de presion de aceite (0 Hay / 1 no hay) B022 1/I3 1/I4 EnP ParB052 Prio = 0 Quit = off Text1: enabled Text2: disabled pantalla de alarma B053 B043 B053/1 B022 B053/2

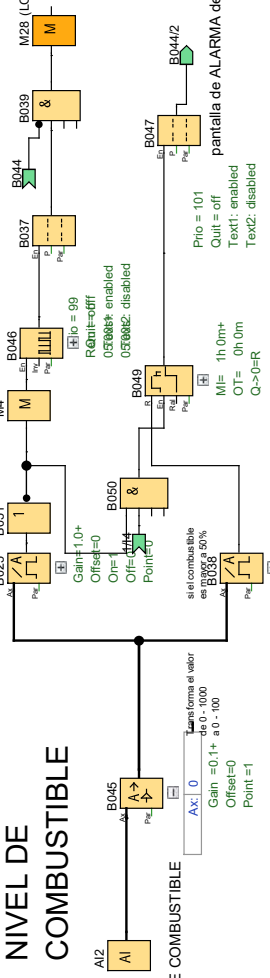
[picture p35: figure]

Q21 = Abrir contactor K3 0 = cerrar contactor K3 High EnP ParB020 Prio = 2 Quit = off Text1: enabled Text2: disabled PANTALLA DEL PLC 1 (PRECION DE ACITE, TEMP MOTOR y TEMP. AMB.) M25 (LOGO! se retroilumina en blanco) EnP ParB033 Prio = 3 Quit = off Text1: enabled Text2: disabled PANTALLA DEL PLC 2 (PRECION DE ACITE, TEMP MOTOR y combustible) En Inv ParB035 Rem = off 10:00s+ 10:00s B036 ALIMENTACION DEL HANGAR CON EL MOTOR PANTALLA DEL PLC B015 TrgT B034 Rem = off 02:00s+ TrgT B019 Rem = off 30:00m+ Ta: 00:00m T: 30:00m TIEMPO DE ESPERA A ESTABILIZACION DE LA RED ANTES DE APAGAR EL MOTOR 1/I3 TrgT B031 Rem = off 05:00m+ 1/I4 1/B032/2

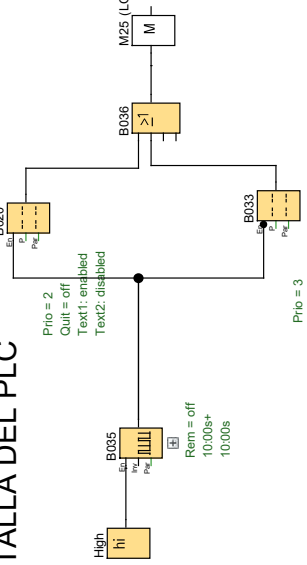
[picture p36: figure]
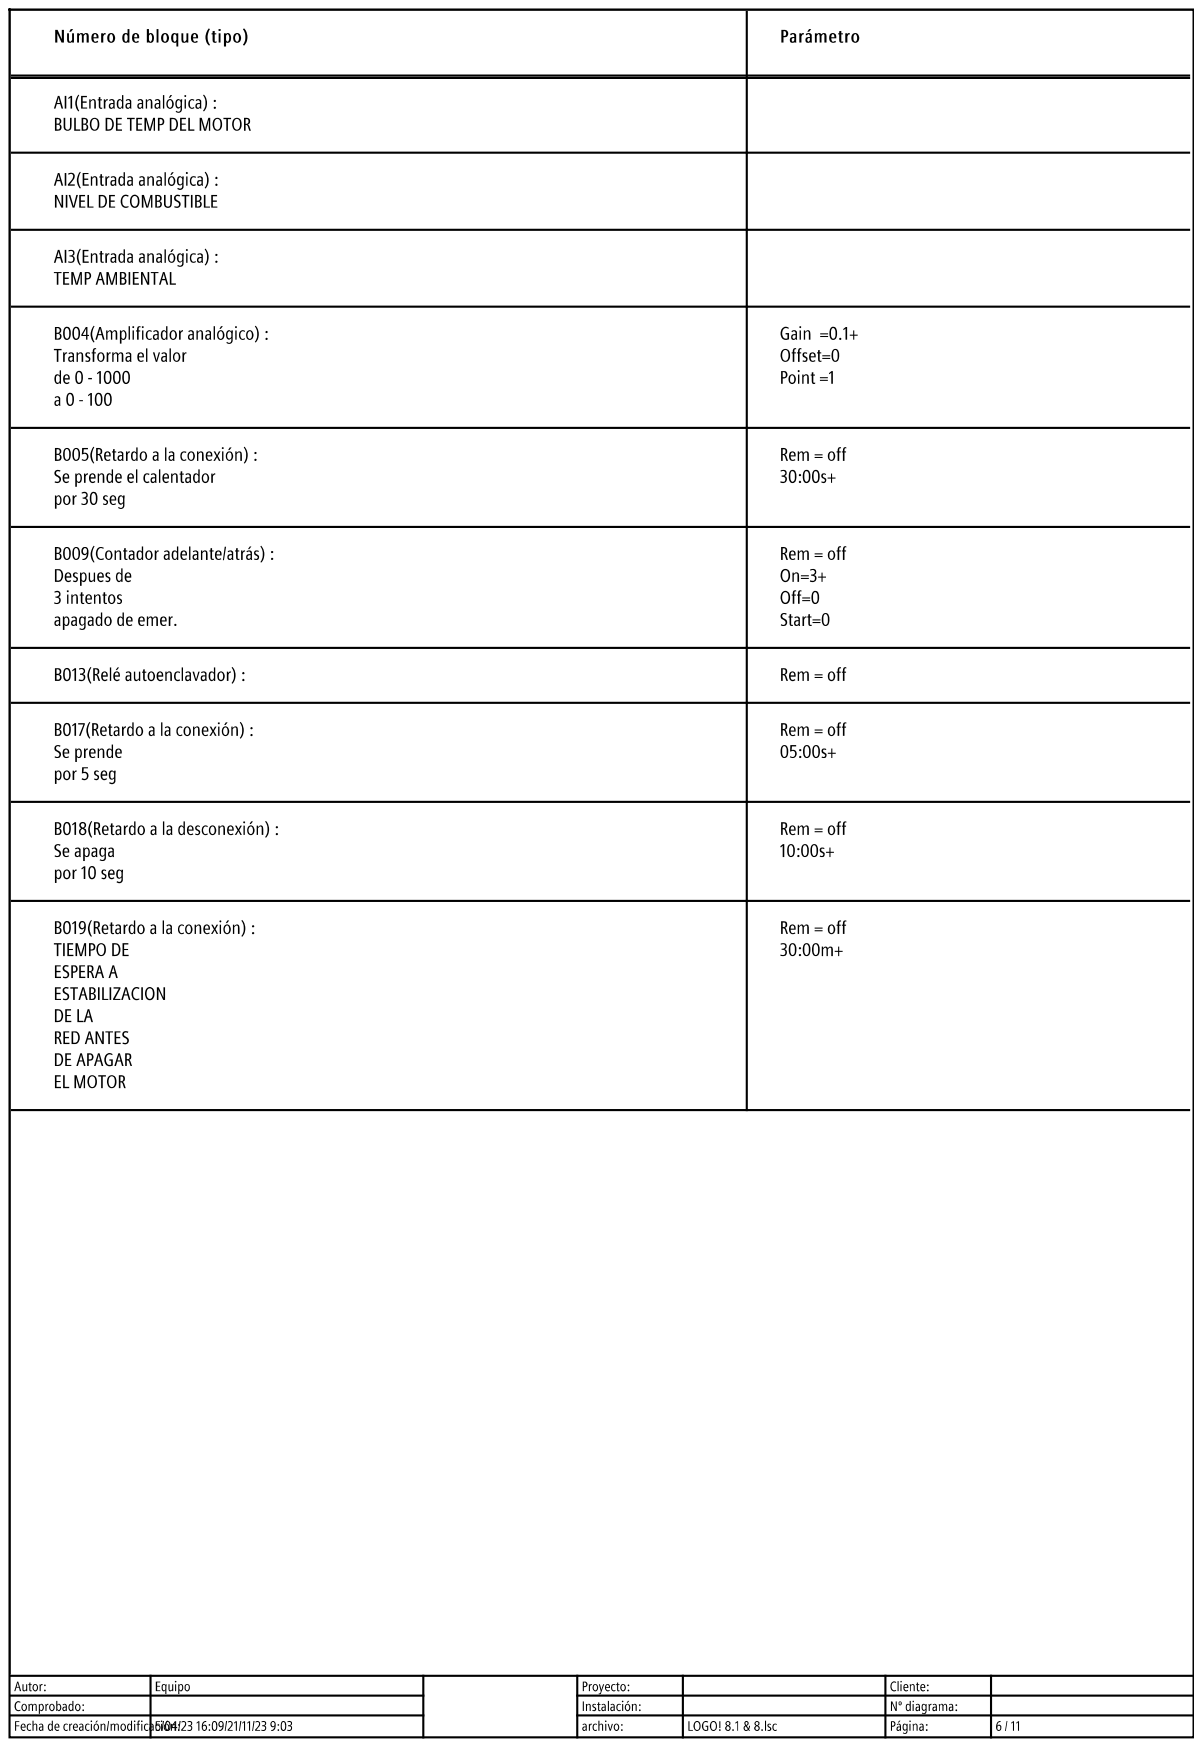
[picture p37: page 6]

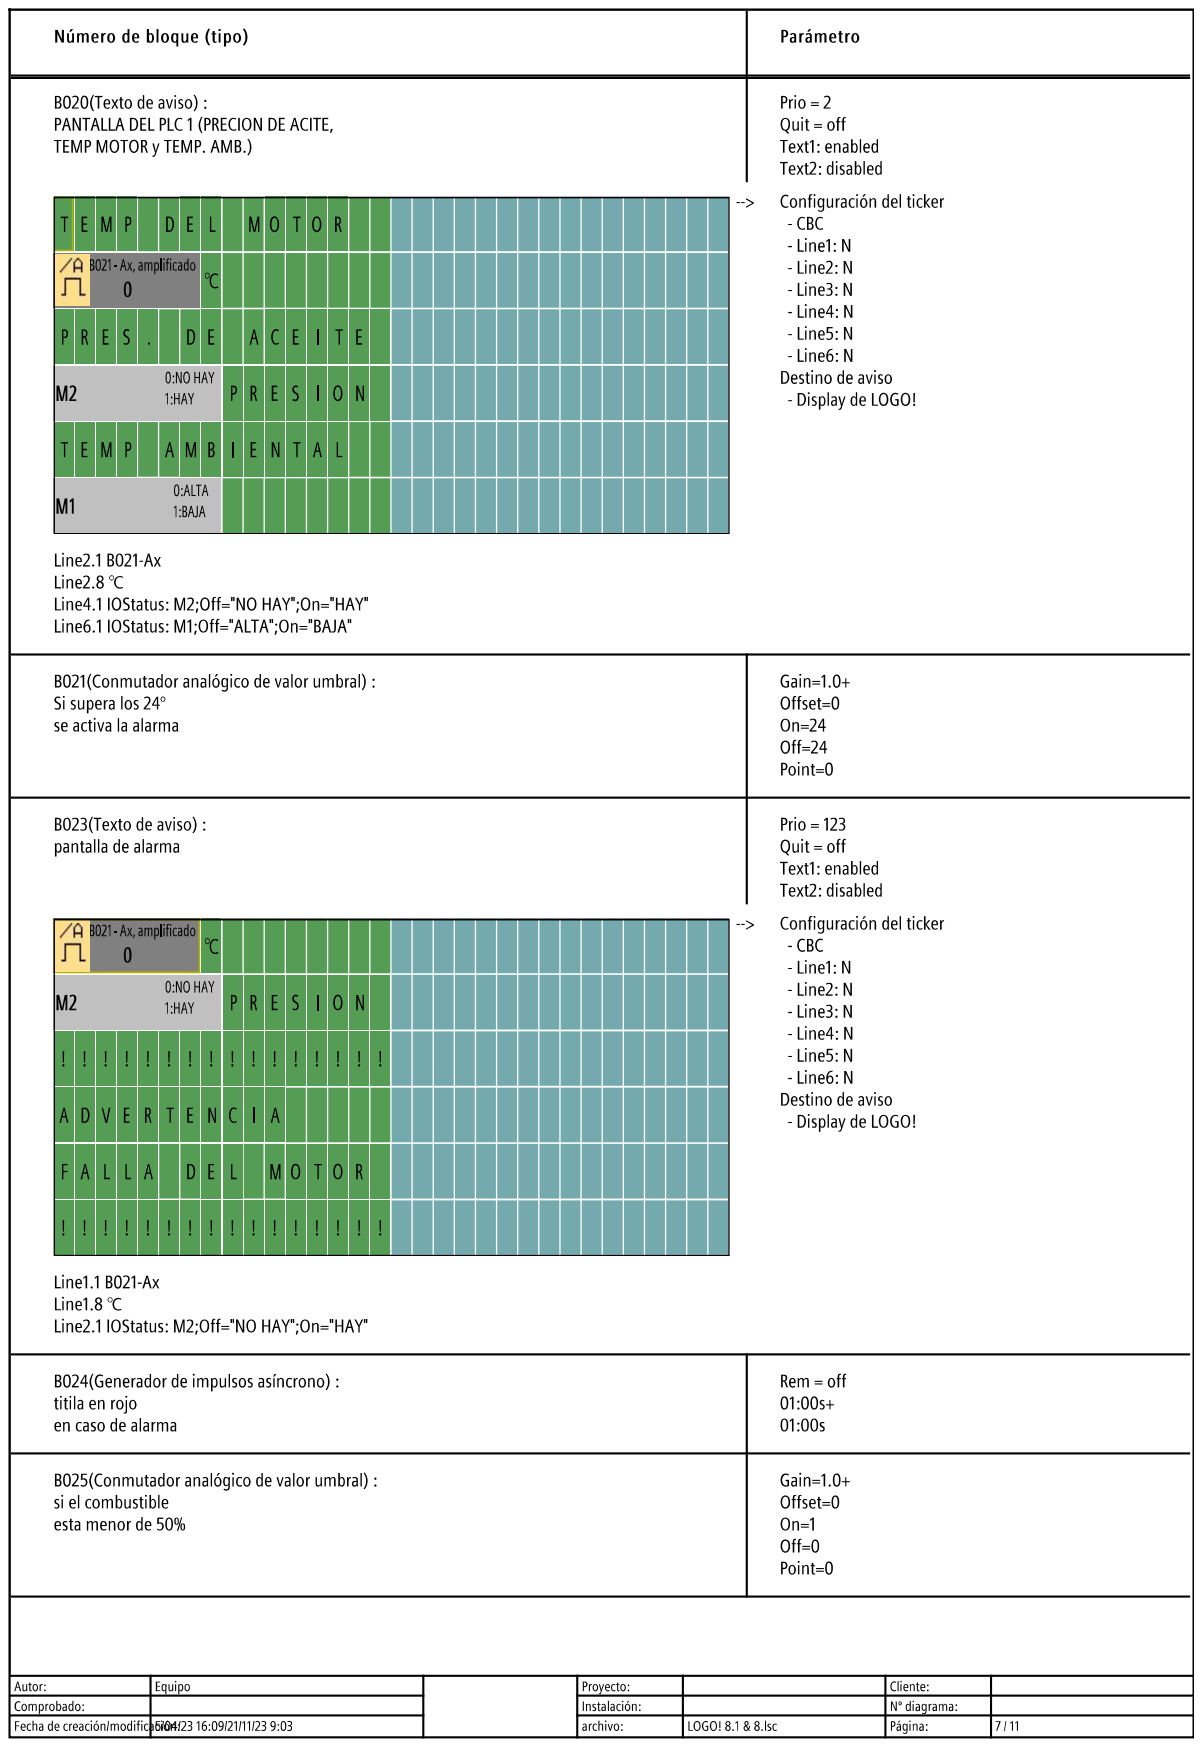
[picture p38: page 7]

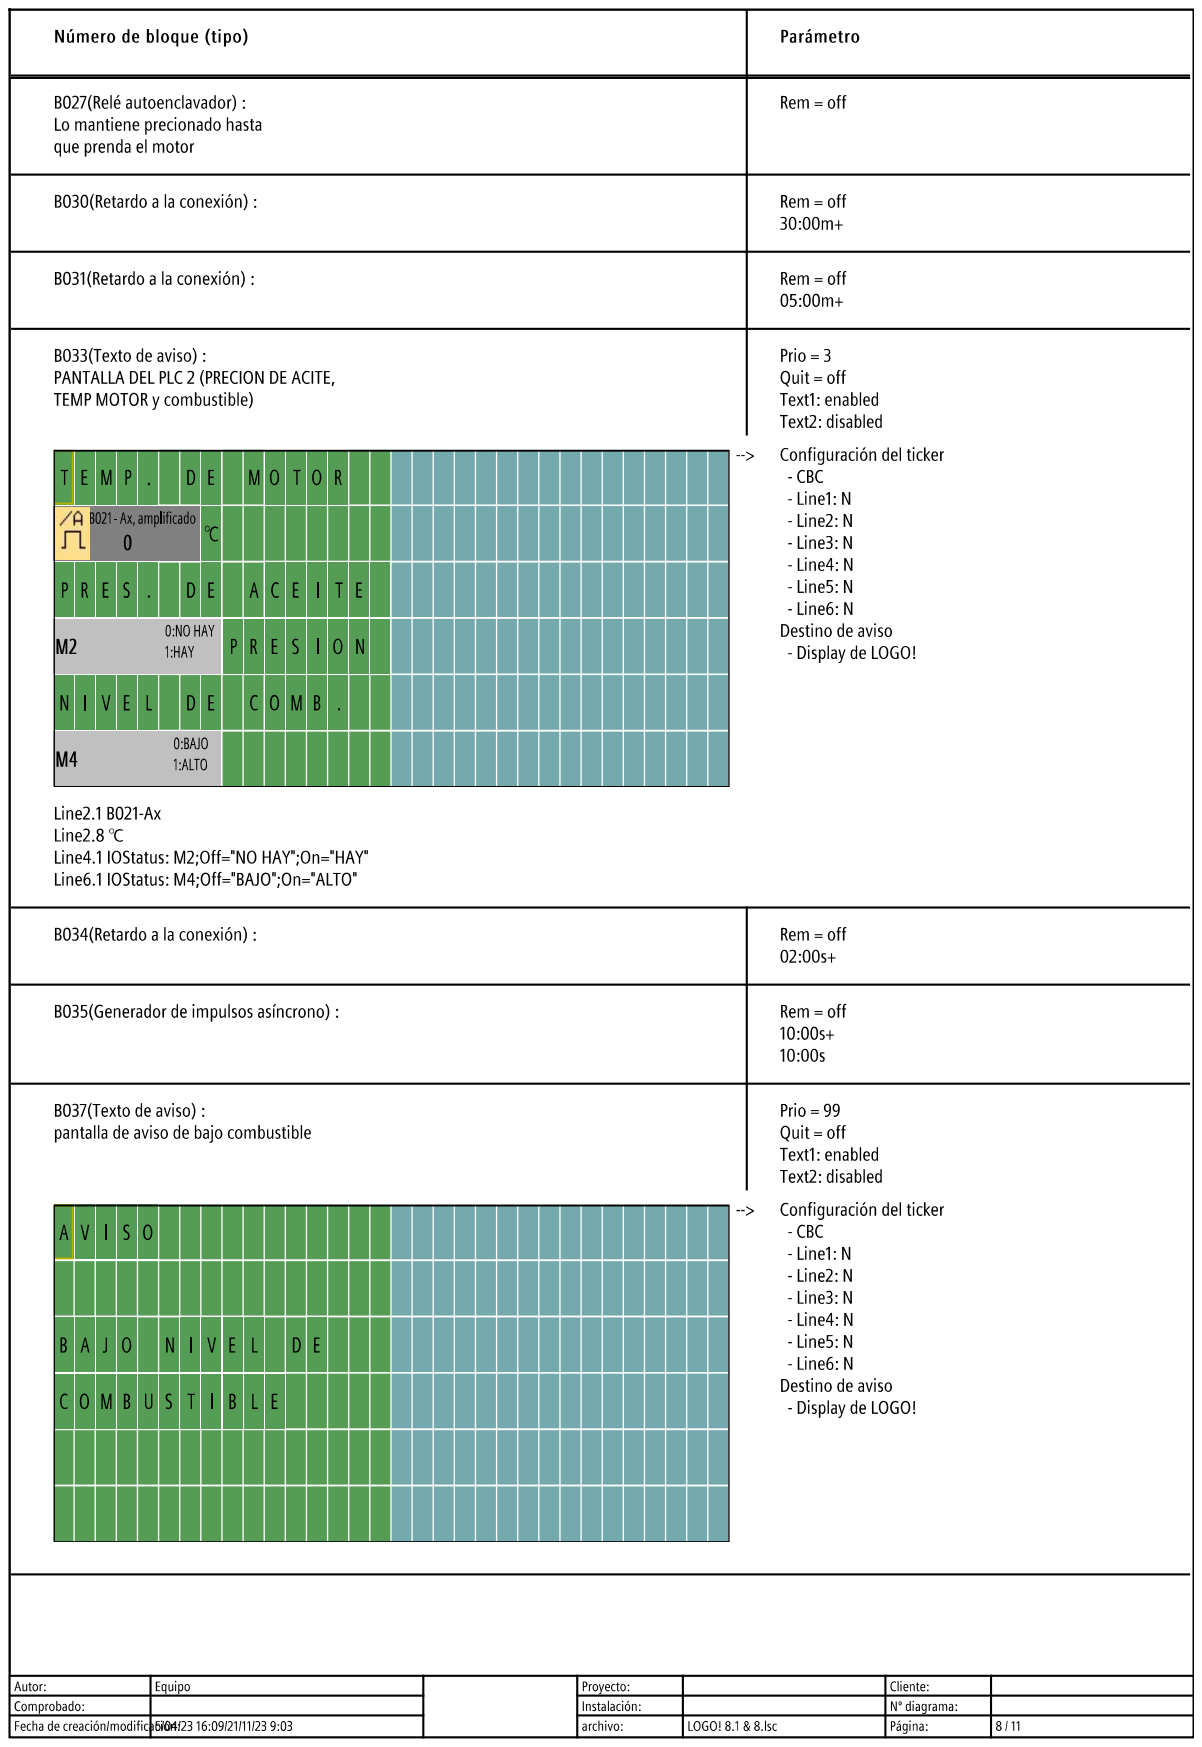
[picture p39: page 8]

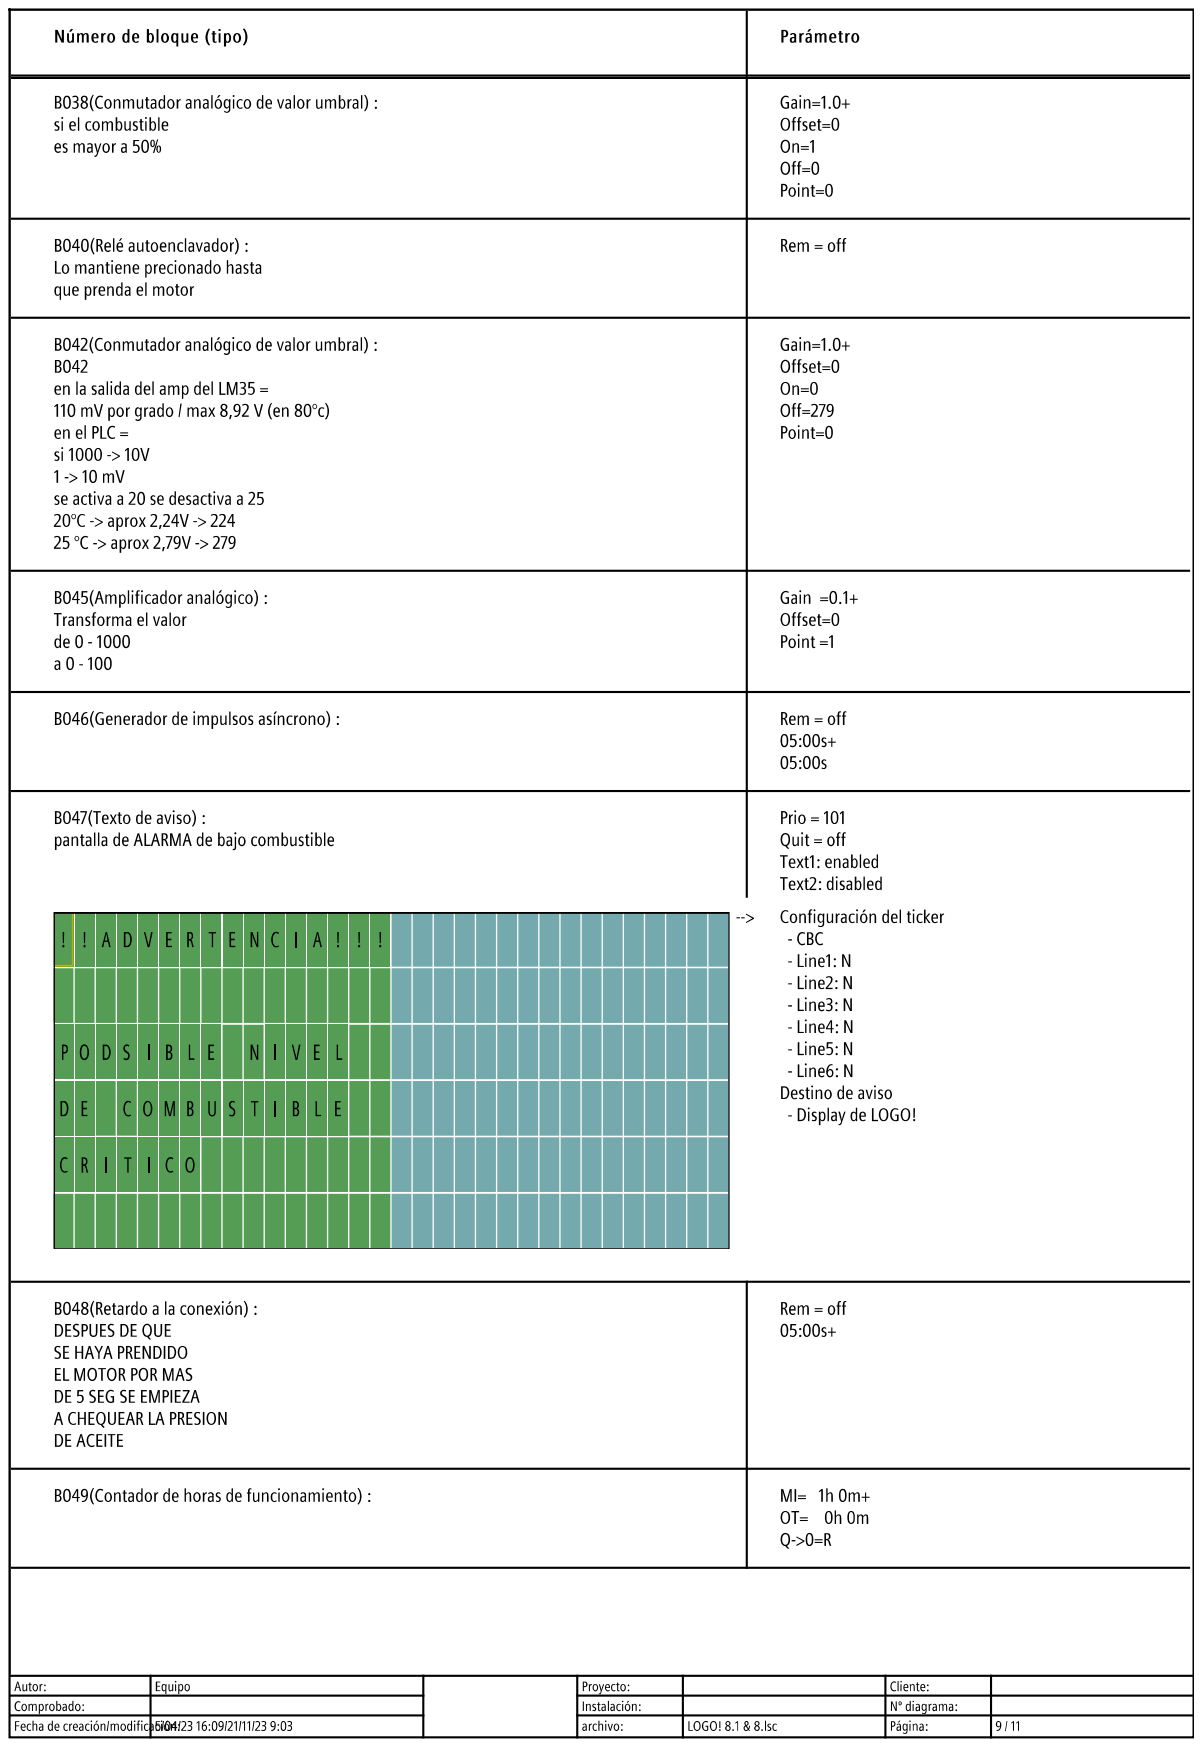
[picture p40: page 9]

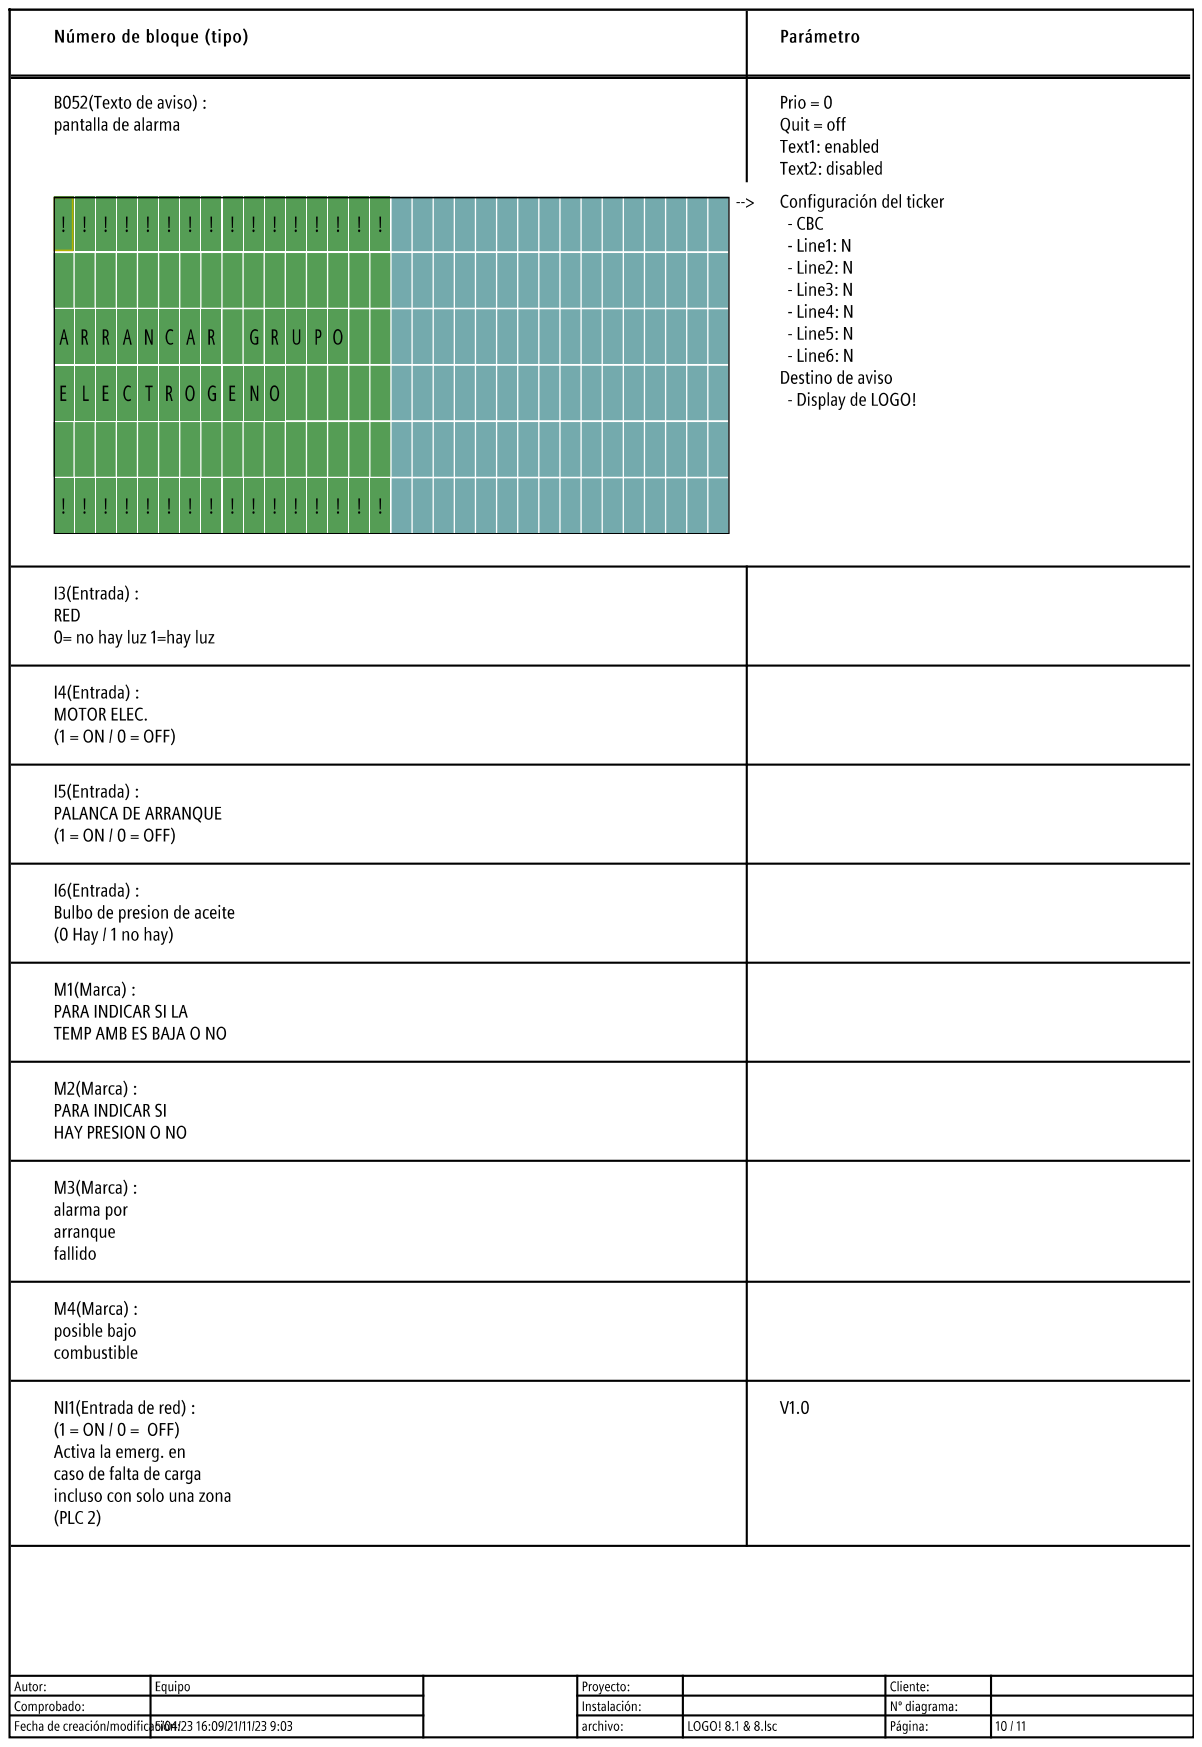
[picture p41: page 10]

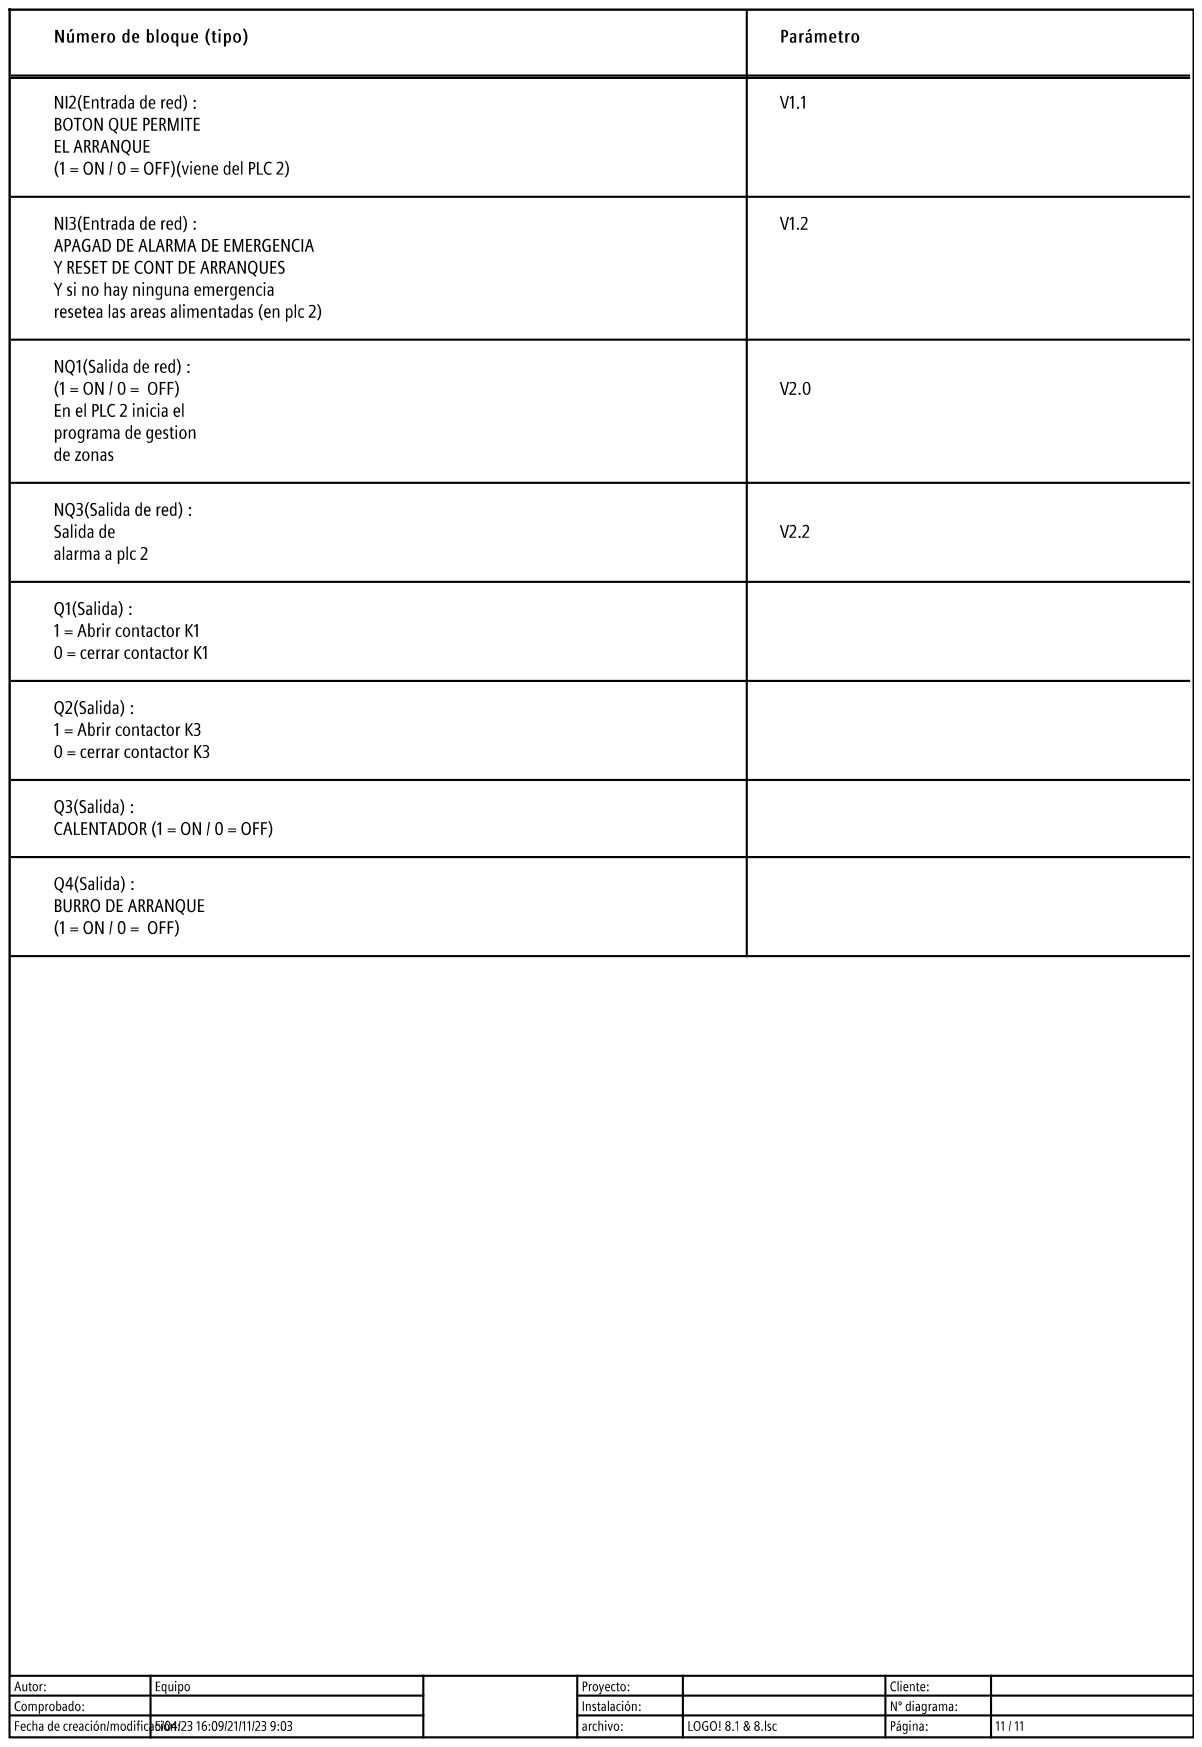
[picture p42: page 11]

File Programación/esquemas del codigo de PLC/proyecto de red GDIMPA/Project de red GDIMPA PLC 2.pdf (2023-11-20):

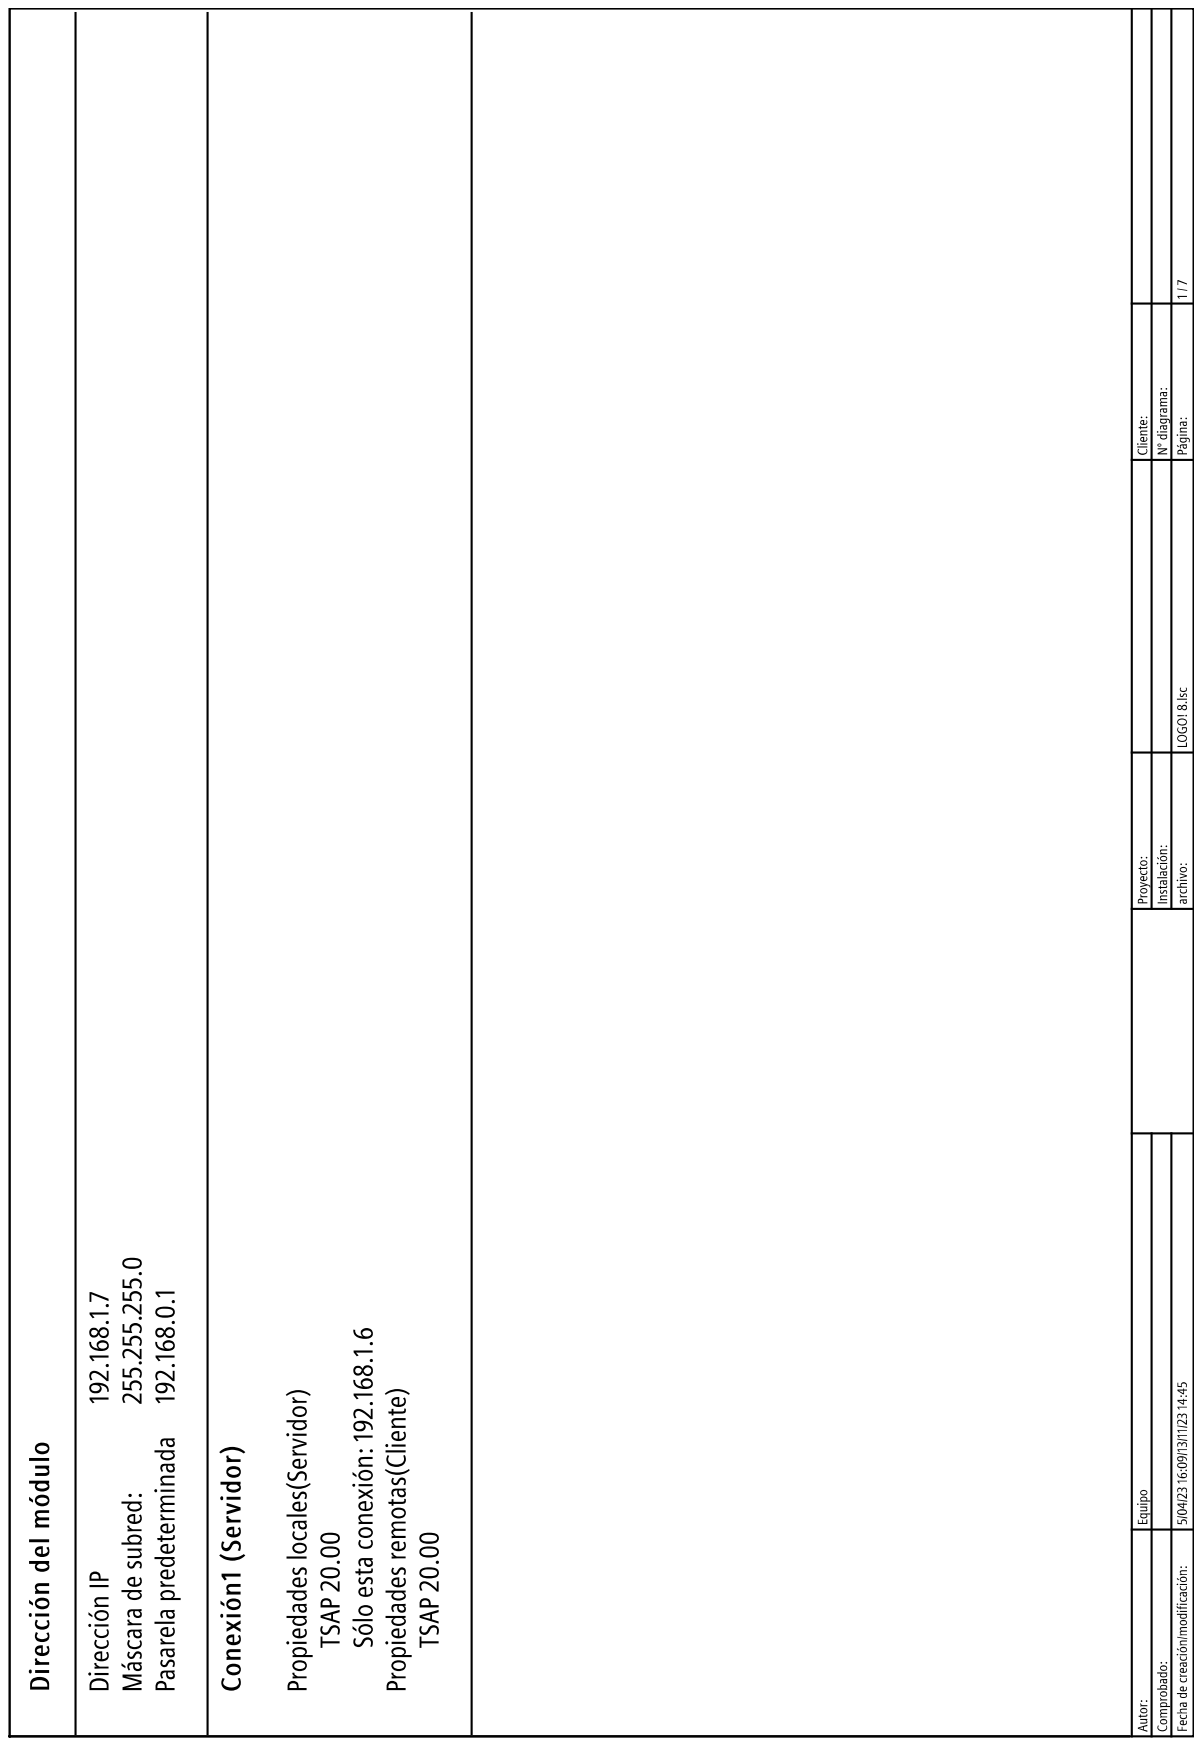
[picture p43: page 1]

Q1 Q2 Activa K9 (para mostrar la fase 1) Activa K10 (junto a Q3 muestran la fase 3) SRParB027 Rem = off B029 SRParB031 Rem = off B033 TrgT B036 Rem = off 05:00s+ Ta: 00:00s T: 05:00s SRParB037 Rem = off B038 B039 B044 TrgT B045 Rem = off 05:00m+ Ta: 00:00m T: 05:00m I1 Falta de carga (1 = no hay falta de carga, 0 = hay falta de carga) M29 (LOGO! se retroilumina en rojo) En Inv ParB001 Rem = off 01:00s+ 01:00s EnP ParB002 Prio = 127 Quit = off Text1: enabled Text2: disabled NI1 V2.0 NQ1 V1.0 2/B006/En 2/B005/En inicia el programa de gestion de zonas (proviene del PLC 1) Se espera por 5 min para que se estabilize el motor Se espera por 5 seg para que se estabilize el motor Activa la alarma en el PLC 1 Pantalla de alarma titila en rojo I3 NQ3 V1.2 APAGAD DE ALARMA DE EMERGENCIA Y RESET DE CONT DE ARRANQUES (en plc 1) Y si no hay ninguna emergencia resetea las areas alimentadas 2/B008/1 B009 TrgT B035 Rem = off 05:00s+ Ta: 00:00s T: 05:00s Se espera por 5 seg para que se estabilize el motor B010 2/M2 2/M3 2/M3 B027 B035/Trg B031 2/B004/1 B036/Trg CONTROL DE ZONAS 2/B003/En High B011 High En Inv ParB012 Rem = off 05:00s+ 05:00s Q3 B013 B014 En Inv ParB016 Rem = off 10:00s+ 05:00s permite mostrar la fase dos X1X2 B027/R I3 I3 B037/R B031/R I3 2/B015/En M1 Para indicar fase 2 alimentada

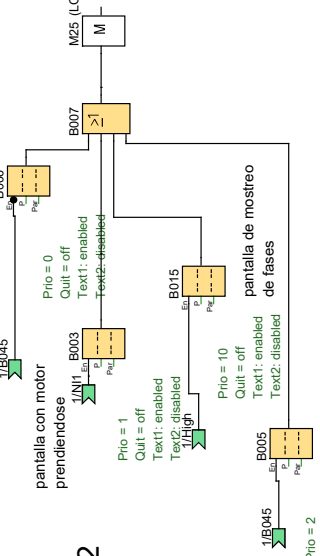
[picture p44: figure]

Activa K10 (junto a Q3 muestran la fase 3) M25 (LOGO! se retroilumina en blanco) EnP ParB005 Prio = 2 Quit = off Text1: enabled Text2: disabled 1/B045 EnP ParB006 Prio = 0 Quit = off Text1: enabled Text2: disabled B007 1/B045 NQ2 V1.1 I2 BOTON QUE PERMITE EL ARRANQUE Va al PLC 1 pantalla con motor apagado pantalla con motor prendido (indica que zonas estan alimentadas) I4I5 Prende media y alta Prende solo alta B004 B008 1/B037 M2 M3 1/B009/1 1/B010/1 1/B009/3 MODO media y altas prendidas MODO alta sola prendida 1/B031 PANTALLA PLC 2 CONTROL DE ZONAS MANUAL boton de arranque NI3 V2.2 Alarma del PLC 1 Q4 luz de alarma EnP ParB003 Prio = 1 Quit = off Text1: enabled Text2: disabled pantalla con motor prendiendose1/NI1 Activa K8 (junto a Q2 muestran la fase 3) luz de alarma EnP ParB015 Prio = 10 Quit = off Text1: enabled Text2: disabled 1/High pantalla de mostreo de fases

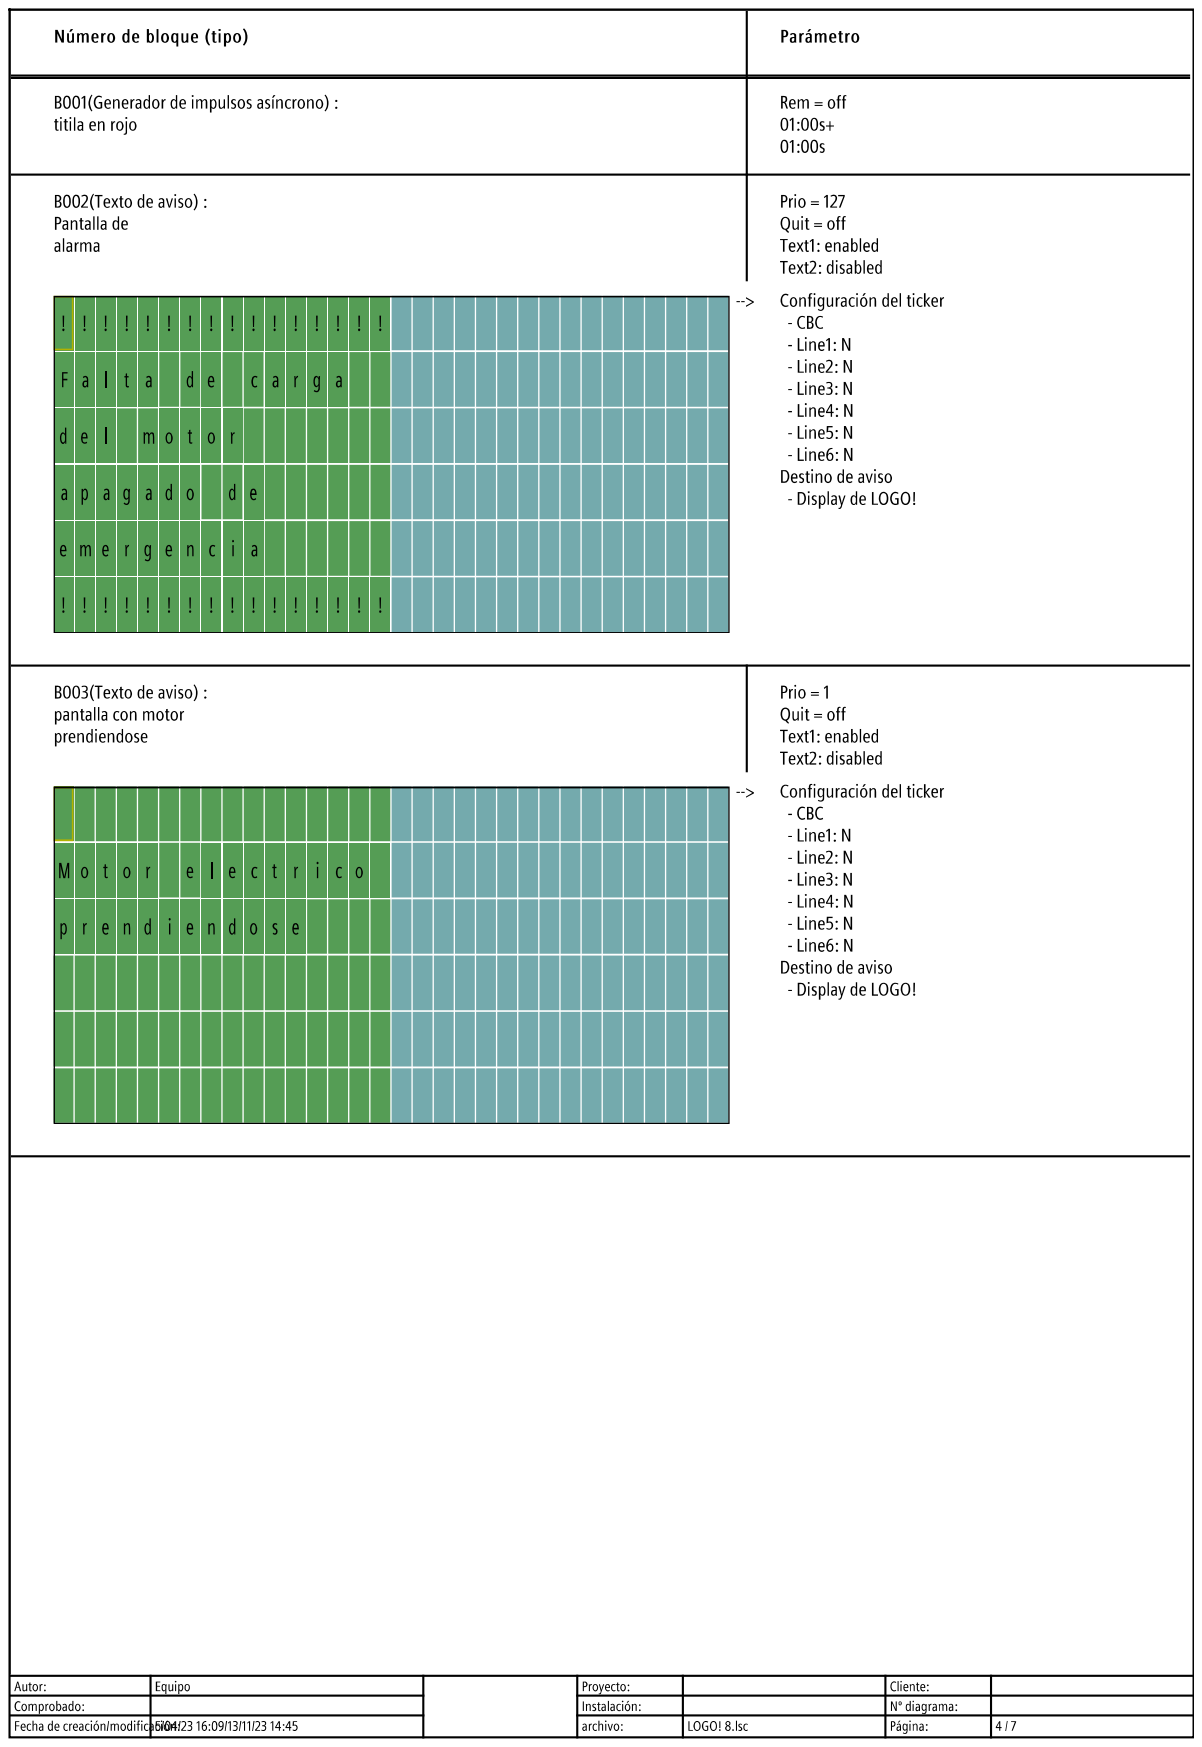
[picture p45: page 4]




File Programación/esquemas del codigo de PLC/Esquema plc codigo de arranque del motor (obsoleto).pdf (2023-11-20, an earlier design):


I1 Q1 BURRO DE ARRANQUE B001 RED 0=hay luz 1=no hy luz I4 MOTOR ELEC. B003 Q3 CALENTADOR TrgT B005 Rem = off 30:00s+ B006 B008 RCnt Dir ParB009 Rem = off On=3+ Off=0 Start=0 B010 I2 APAGAD DE ALARMA DE EMERGENCIA Y RESET DE CONT DE ARRANQUES Y si no hay ninguna emergencia resetea las areas alimentadas Q4 B011 ALARMA DE EMERGENCIA B012 SRParB013 Rem = off B014 Q2 B015 1 = CORTAR MOTOR DIESEL 0 = NO CORTAR MOTOR DIESEL B016 TrgT B017 Rem = off 05:00s+TrgRT B018 Rem = off 10:00s+ I3 BOTON DE ARRANQUE B007 TrgT B019 Rem = off 05:00s+ Ta: 00:00s T: 05:00s TIEMPO DE ESPERA A ESTABILIZACION DE LA RED ANTES DE APAGAR EL MOTOR AI1 BULBO DE TEMP DEL MOTOR AI2 BUBLO DE PRECION DE ACEITE High Ax ParB021 Gain=1.0+ Offset=0 On=903 Off=903 Point=0 B022 En Inv ParB024 Rem = off 01:00s+ 01:00s M29 (LOGO! se retroilumina en rojo) EnP ParB023 Prio = 123 Quit = off Text1: enabled Text2: disabled X2 EnP ParB020 Prio = 2 Quit = off Text1: enabled Text2: disabled PANTALLA DEL PLC 1 (PRECION DE ACITE Y TEMP MOTOR) SRParB040 Rem = off B041 AI3 TEMP AMBIENTAL Ax ParB042 Gain=1.0+ Offset=0 On=224 Off=279 Point=0 Ax ParB002 Gain=1.0+ Offset=0 On=250 Off=250 Point=0 ESTA EN PSI On: 250 Off: 250 Ax: 0 B043 B025 B022/3 B025 B015/1 I1 Q4 B022/4 B034 en la salida del amp del LM35 = 110 mV por grado / max 8,92 V (en 80°c) en el PLC = si 1000 -> 10V 1 -> 10 mV se activa a 20 se desactiva a 25 20°C -> aprox 2,24V -> 224 25 °C -> aprox 2,79V -> 279 NI1 IP: 192.168.1.6 TSAP: 20.00,00.00 LOGO! 8.3 Q1 NI1 B043/3 NQ1 IP: 192.168.1.6 TSAP: 20.00,00.00 LOGO! 8.3 I1 NQ2 IP: 192.168.1.6 TSAP: 20.00,00.00 LOGO! 8.3 I2 NQ2/1 I2 NQ1/1 I4




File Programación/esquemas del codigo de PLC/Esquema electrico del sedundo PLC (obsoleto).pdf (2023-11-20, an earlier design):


Q1 Q2 Desactivo area de baja prioridad Desactivo area de media prioridad SRParB027 Rem = off B029 SRParB031 Rem = off TrgT B035 Rem = off 05:00s+ B033 TrgT B036 Rem = off 05:00s+ Ta: 00:00s T: 05:00s SRParB037 Rem = off B038 B039 B044 TrgT B045 Rem = off 05:00s+ el el codigo de gestion de zonas tiene que entrar I4 e I2 y salir a B034/2 y B043/3 NI1 NI2 IP: 192.168.1.1 TSAP: 21.00,21.00 LOGO! 8.3 Q2 ajustar con dispositivo remoto a I4ajustar con dispositivo remoto a I2 NQ1 IP: 192.168.1.1 TSAP: 21.00,21.00 LOGO! 8.3 I1ajustar con dispositivo remoto a B034/2 I1 Falta de carga (1 = no hay falta de carga, 0 = hay falta de carga) M29 (LOGO! se retroilumina en rojo) En Inv ParB001 Rem = off 01:00s+ 01:00s EnP ParB002 Prio = 127 Quit = off Text1: enabled Text2: disabled EnP ParB003 Prio = 1 Quit = off Text1: enabled Text2: disabledEnP ParB004 Prio = 2 Quit = off Text1: enabled Text2: disabled M25 (LOGO! se retroilumina en blanco) High EnP ParB005 Prio = 0 Quit = off Text1: enabled Text2: disabled X1 X2




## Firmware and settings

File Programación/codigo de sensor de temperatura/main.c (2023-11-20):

#include <LiquidCrystal_I2C.h>
#include <Wire.h> 

LiquidCrystal_I2C lcd(0x3F,20,4);  // set the LCD address to 0x27 for a 16 chars and 2 line display

const int sensorPin = A0; // Pin del sensor de temperatura LM35 conectado a A0

void setup() {
  lcd.init();
  // Print a message to the LCD.
  lcd.backlight();
}

void loop()
{
  int sensorValue = analogRead(sensorPin); // Lee el valor del sensor LM35
  float temperatureC = (((sensor * 5.0)/1024)/100)/ 9; // Convierte el valor a temperatura en grados Celsius
  lcd.clear(); // Borra el contenido anterior del LCD
  lcd.setCursor(0, 0); // Posiciona el cursor en la primera fila, primera columna
  lcd.print("Temperatura: "); // Muestra el texto "Temperatura: " en el LCD
  lcd.setCursor(0,1); // Posiciona el cursor en la segunda fila, primera columna
  lcd.print(temperatureC);// Muestra la temperatura en el LCD
  lcd.print(" C +/- 1C");  // Muestra el símbolo de grados Celsius en el LCD
  delay (1000);  // Espera 1 segundo antes de volver a leer el sensor
}//fue hecho atravez de arduino

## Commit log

2023-10-25 feat: agregar código de arranque del motor
2023-10-25 feat: agregar codigo de arduino
    codigo de arduino para mostrar temperatura en pantalla
2023-10-31 feat: agregar codigo de temp. amb. del motor
2023-10-31 feat: agregar código de apagado automatico
2023-10-31 feat: agregar código de gestión de zonas
2023-10-31 feat: agregar sensores de temp y presión de aceite
2023-10-31 feat: agregar código de pantalla de alarma
2023-10-31 feat: agregar pantalla de muestra de datos
2023-10-31 fix: arreglar codigo de temp. ambiental
    solo era necesario una salida, no dos
2023-10-31 feat: agregar mas pantallas de PLC
2023-11-08 fix: simplificar codigo de pantalla del PLC
    No eran necesarias tantas pantallas
2023-11-08 feat: agregar codigo de comunicacion por ethernet
    Codigo del PLC 1 para comunicarse por ethernet con el PLC 2
2023-11-08 feat: agregar codigo del PLC 2
    Codigo encargado de la gestion de zonas
2023-11-08 feat: agregar codigo de proyecto de red
    El proyecto de red permitira codificar la comunicacion entre los plc a traves de cable athernet de forma simple y funcional
2023-11-08 feat: agregar codigo de comunicacion por ethernet
    Gracias a que es un proyecto de red es mucho mas facil comprobar su funcionamiento
2023-11-08 feat: agregar codigo del PLC 2 al proyecto de red
    Se agrago el codigo del plc 2 al proyecto de red con el codigo de comunicacion por cable ethernet ya implementado.
2023-11-08 fix: Mover y cambiar entrada de presion de aceite
    Se movio al plc 2 la entrada de presion de aceite para liberar una entrada en el plc 1 para el medidor de combustible. Tambien se modifico la entrada de presion de aceite para que sea una entrada digital.
2023-11-08 refactor: Se cambio el nombre de codigos obsoletos
2023-11-08 feat: agregar codigo de nivel de combustible
2023-11-08 feat: agregar pantalla 2 en el plc 1
    Se agrego una segunda pantalla que se intercala con la primera para mostrar todos los datos del plc 1
2023-11-08 feat: agregar botones de apagado manual de zonas
    Se agregaron botones para apagar las zonas manualmente, estos tienen menor prioridad que el sistema de apagado automatico debido a falta de carga
2023-11-08 refactor: Pasar en limpio el codigo y comentarios
    Se paso en en limpio el codigo para que se pueda leer mas facil, y se agregaron comentarios.
2023-11-08 fix: Modificar codigo de nivel de combustible
    Se arreglo el codigo de nivel de combustible para que funcione como deberia
2023-11-08 feat: agregar libreria wire.h
2023-11-08 fix: modificar funcion de seteo del lcd
    La anterior funcion no era la correcta para la plaqueta
    [main.c]
2023-11-08 refactor: arreglar comentario
    Para una explicacion mas facil
    [main.c]
2023-11-08 fix: Remplazar biblioteca
    La anterior biblioteca era para lm34
    [main.c]
2023-11-08 fix: mover de lugar las variables
    [main.c]
2023-11-08 fix: Cambiar seteo de variable
    Porque se cambio de biblioteca
    [main.c]
2023-11-08 refactor: optimizar seteo de variable
    Esto para optimizar el codigo
2023-11-08 fix:Arreglar valores de variable temp.C
    [main.c]
2023-11-08 fix: arreglar nombre de variable
    Esto debido a la nueva bilbioteca
    [main.c]
2023-11-08 feat: Conectar el lm35 atravez del arduino
2023-11-08 Fix: Arreglar conexión con el LCD
    [main.c]
2023-11-08 feat: Agregar codigo de posicionamiento de cursor
2023-11-08 feat: Agregar la simbología de grado
2023-11-08 feat: agregar codigo para mostrar lectura
    No se porque, pero si elimino esto no funciona el lcd
2023-11-08 fix: borrar códigos innecesario
    [main.c]
2023-11-08 fix: borrar codigo innecerario
    [main.c]
2023-11-08 fix: arreglar fallo de calculo
    El calculo era incorrecto, debido a que estaba conectado a salida de un amplificador.
    [main.c]
2023-11-08 style: Clarificar margen de error en pantalla
    [main.c]
2023-11-09 fix:remplazar corte de motor, Invertir entrada red
    Se reemplazo la parte del código que cortaba el motor con la apertura y cierre del contactor K3, además se invirtió la entrada de red
2023-11-09 fix: Modificar codigo de alarma
    Se modifico el código de alarma y se movió la salida de alarma al plc 2 debido que ya se estaban utilizando todas las salidas del plc 1 por otras salidas
2023-11-09 feat: agregar retardo a prendido de K3
    Se agrego un retardo de 5 min a la conexión de K3
2023-11-13 fix: cambiar varios detalles del plc 1 y 2
    Se movio boton de apagado de alarma a plc 2, presion de aceite a plc 2, se agutaron, agragaron y eliminaron varios retardos en la activacion y apagado de los contactores K1 y K3, entre otros pequeños ajustes
2023-11-13 feat: agregar mostreo de fase 1, 2 y 3
    Se lo agrego en el plc 2, debido a falta de salidas se desconecto el programa gestion de zonas, no se lo borro debido a un posible uso futuro
2023-11-13 feat: agregar pantalla de muestreo de fase
2023-11-15 docs: agregar carpeta de campo
2023-11-15 feat: agregar imagen de integrantes en readme
2023-11-15 feat: agregar diseño de la placa rectificadora
2023-11-15 feat: agregar imagenes del proceso de la placa
    se agregaron imagenes de proceso de creacion de la placa rectificadora.
2023-11-15 feat: agregar nombres y links de los integrantes
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2023-11-15 feat: agregar proceso del soporte del tablero
    Se agrego el seguimiento de los procesos del soporte (pintara, corte, soldadura al motor)
2023-11-15 feat: agregar proceso de limpieza y desarmado
    Se realizo un mantenimiento (limpieza y chequeo) de la bomba eyectora, incluyendo la revision de marcha / parada.
2023-11-15 feat: Agregar Limpieza del tubo del motor
    Se realiza un chequeo del tubo del motor para su restauracion
2023-11-15 feat: agregar imagenes del proceso del radiador
    Se hizo un proceso de revision para comprobar su estado actual
2023-11-15 feat: agregar imagen del sistema de gasoil
    Al igual que otro elementos de la maquina, se realizo una revision y estado del proyecto.
2023-11-16 style: Pasaje de la carpeta técnica a Canva
2023-11-21 feat: agregar modelado de soporte del medidor comb
    se agrego el modelado 3D del soporte del medidor de combustible
    [Soporte reloj de combustile.dwg, Soporte reloj de combustile.stl]
2023-11-21 feat: agregar modelado 3D tablero elec. y soporte
    Se agrego el modelado 3D del tablero eléctrico y de su soporte
    [tablero y soporte.dwg]
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2023-11-21 fix: ajustar tiempos de prendido y corte de K1 y 3
    se ajustaron los tiempos de prendido y corte de los contactores
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2023-11-21 Fix: se arreglo la prioridad de una pantalla
2023-11-21 feat: robar esta mal guzman no agarres el trabajo de otros
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2023-11-21 fix: agregar logos de patrocinadores faltantes
2023-11-21 feat: agregar foto circuito elec del sensor temp
    se agrego la foto del circuito eléctrico del sensor de temperatura funcional
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2023-11-23 refactor: Terminar de ordenar carpetas
    [Soporte reloj de combustile.dwg, Soporte reloj de combustile.stl, tablero y soporte.dwg]
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2023-11-23 feat: Agregar archivo e imagen del esquema del circuito electrico
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2023-11-23 feat: conectar la salida del tanque a la bomba
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2023-11-23 feat: conectar flotante a la bateria y reloj
2023-11-23 feat: terminar instalación del sistema del tanque
    termine de instalar el sistema del tanque de combustible
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2023-11-23 feat: agregar fotos de cableado de cambio de fases
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2023-11-23 feat: cablear bulbo de temperatura con el tablero
2023-11-23 feat: agregar imagen de inicio del cableado del tablero
2023-11-26 fix: corregir link en el readme
